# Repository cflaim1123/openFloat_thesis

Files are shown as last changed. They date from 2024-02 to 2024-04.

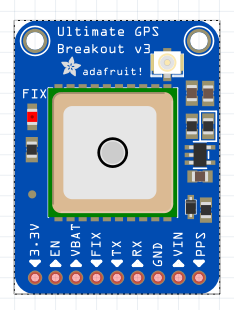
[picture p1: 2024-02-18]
floatBuild/electronics/floatElectronicsFritzingPics/Screenshot 2023-10-19 at 9.54.05 PM.png

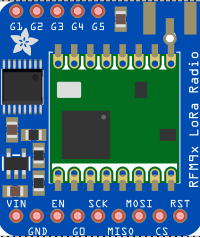
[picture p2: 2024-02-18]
floatBuild/electronics/floatElectronicsFritzingPics/Screenshot 2023-10-19 at 10.49.54 PM.png

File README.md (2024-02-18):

# openFloat
This repository documents the build and implementation of a DIY profiling float for my undergraduate senior thesis at the University of Washington School of Oceanography.
To clone this repository to your working directory, paste the following line into your terminal or command line:
```
git clone https://github.com/cflaim1123/openFloat_thesis.git
```
If you do not have git installed on your machine, follow this [link](https://git-scm.com/downloads) to the git website. 

## Project description
Ocean salinity, a measure of salt concentration in seawater, is a key variable influencing water density and controls important processes like mixing and stratification. Temporal and spatial salinity variability is high in dynamic coastal systems like Puget Sound, which can present a challenge for making salinity measurements that can characterize this variability. Salinity is typically measured using conductivity cells, a sensor that quantifies electrical current through seawater. These sensors can be deployed on ship-based CTDs, spatially-limited moorings, or costly AUVs and can have limited long-term stability. This project, therefore, proposes the development of a cost-efficient DIY profiling float for salinity estimation by way of back-calculation from the TEOS-10 equation of state of seawater. This calculation will be made from known float properties – float density at neutral buoyancy which equals surrounding seawater density – and the in-situ measurement of pressure and temperature via float sensors. This project aims to develop and validate a cost-effective profiling float from common materials with the potential application to increase data resolution in spatially and temporally dynamic estuary systems. For the proof of concept, the float will be deployed alongside a Seaglider in Colvos Passage, WA, for data validation. Unlike many areas of dynamic coastal ecosystems, Colvos Passage experiences high levels of mixing due to local bathymetry and poses as a unique validation site for float development since there is limited spatial variability, making cross-comparison of with the Seaglider easier. This ensures that salinity calculations from the float can be compared to Seaglider data in the same parcel of water to determine the float’s salinity estimation accuracy compared to an industry-standard method for measuring salinity.  

The openFloat will collect pressure and temperature, GPS location, lux, temperature, internal humidity, internal temperature, and internal pressure data. All data will be written to an onboard SD card and transmitted to an onshore radio controller via 915 mHz LoRa (long-range) radio. A digital Onshape CAD model of the openFloat can be found [here](https://cad.onshape.com/documents/a3a60be64346f3ab3cbba062/w/3aa2cdeafc929d436fb9bbdd/e/518a3778be8193c016e5ac27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).

## openFloat Materials
The openFloat is built from 3D-printed and stock hardware and electronics; all parts can be 3D-printed or easily purchased from websites such as [McMaster-Carr](https://www.mcmaster.com/), [Adafruit](https://www.adafruit.com/), [Amazon](https://www.amazon.com/), or [Digikey](https://www.digikey.com/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).

A complete parts and STL file list can be found in this repo's "floatBuild" directory. 

## openFloat Project Concept
The openFloat aims to increase data resolution in dynamic systems by cost-effectively measuring traditional oceanographic data such as temperature, pressure, and salinity. Salinity is not traditionally cheap to measure (e.g., a decent conductivity cell costs ~$5,000).

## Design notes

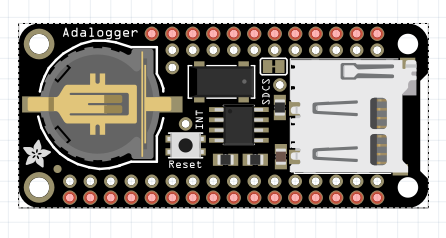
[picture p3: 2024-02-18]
floatBuild/electronics/floatElectronicsFritzingPics/Screenshot 2023-10-19 at 9.54.43 PM.png

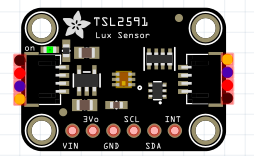
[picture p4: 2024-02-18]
floatBuild/electronics/floatElectronicsFritzingPics/Screenshot 2023-10-19 at 10.00.33 PM.png

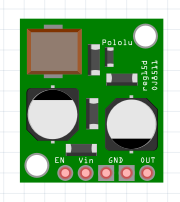
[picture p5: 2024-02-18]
floatBuild/electronics/floatElectronicsFritzingPics/Screenshot 2023-10-19 at 9.55.57 PM.png

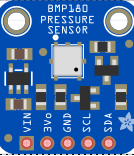
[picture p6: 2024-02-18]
floatBuild/electronics/floatElectronicsFritzingPics/Screenshot 2023-10-20 at 12.47.39 AM.png

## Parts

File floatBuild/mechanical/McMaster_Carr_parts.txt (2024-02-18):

- SCH40 4" PVC pipe (40" length) --> can be bought from any hardware store
- SCH40 4" PVC pipe (9" length?) --> can be bought from any hardware store
- SCH40 1" PVC pipe (25' length) --> can be bought from any hardware store
- 2x Union Straight Connector, 4 Socket-Connect Female (part: 4880K309) 
- 1x Cap, White, 4 Pipe Size Socket-Connect Female (part: 4880K58)
- 1x Bushing Reducing Adapter, 4 Socket Male x 1 Socket Female (part: 4880K072)
- 1x Union Straight Connector, 1 Socket-Connect Female (part: 4880K303)

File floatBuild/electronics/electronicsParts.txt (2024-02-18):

Adafruit 9dof website: https://learn.adafruit.com/adafruit-bno055-absolute-orientation-sensor/arduino-code 

Adafruit pcf8523 RTC: https://learn.adafruit.com/adafruit-adalogger-featherwing/adafruit2-rtc-with-arduino

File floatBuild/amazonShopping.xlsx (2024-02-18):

Store | Item name | Qauntity | total price | link
Amazon | 2-part 24hr epoxy | 1 | 64.89 | https://www.amazon.com/dp/B08XF92PKY
 | 27:1 Geared stepper motor | 1 | 41.91 | https://www.amazon.com/27-Planetary-Gearbox-Stepper-Printer/dp/B00QEUZ9EM
 | TR8x2 800mm lead screw with colar | 1 | 24.99 | https://www.amazon.com/ReliaBot-380mm-Thread-Printer-Machine/dp/B08DJ9JQ6M?s=industrial
 | Tr8x2 brass nut | 1 | 4.99 | https://www.amazon.com/ReliaBot-380mm-Thread-Printer-Machine/dp/B07TZCHP1N?s=industrial
 | TMC2209 stepper drivers | 1 | 26.99 | https://www.amazon.com/BIGTREETECH-Printer-Stepstick-TMC2209-Heatsink/dp/B07YW7BM68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
 | Punching balloon | 1 | 8.39 | https://www.amazon.com/GOLF-Balloons-Assorted-Punching-Wedding/dp/B07F6BFF95
 | 1 gal mineral oil | 1 | 29.99 | https://www.amazon.com/Mineral-Cutting-Butcher-Stainless-Approved/dp/B00VNI1JI0?s=hi
 |  | total: | 202.15

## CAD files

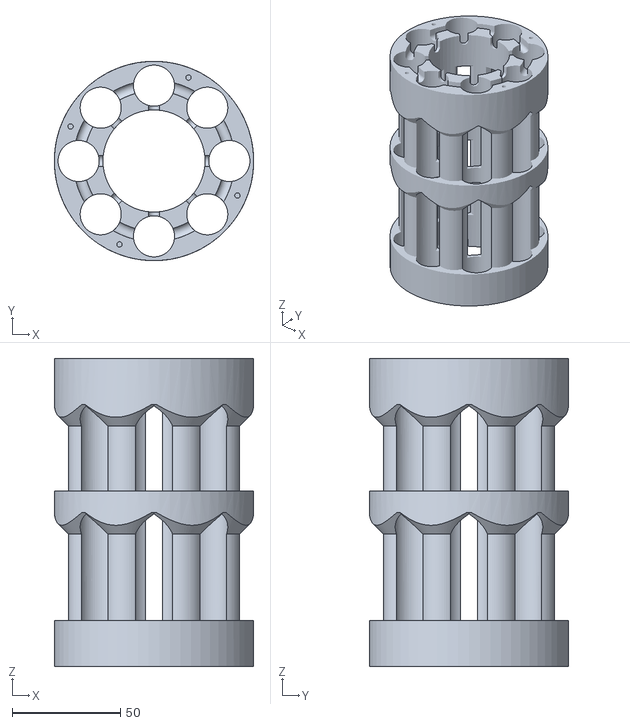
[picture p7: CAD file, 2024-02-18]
floatBuild/mechanical/STLsForPrinting/batteryHolder.stl
92.3 x 92.2 x 142.5

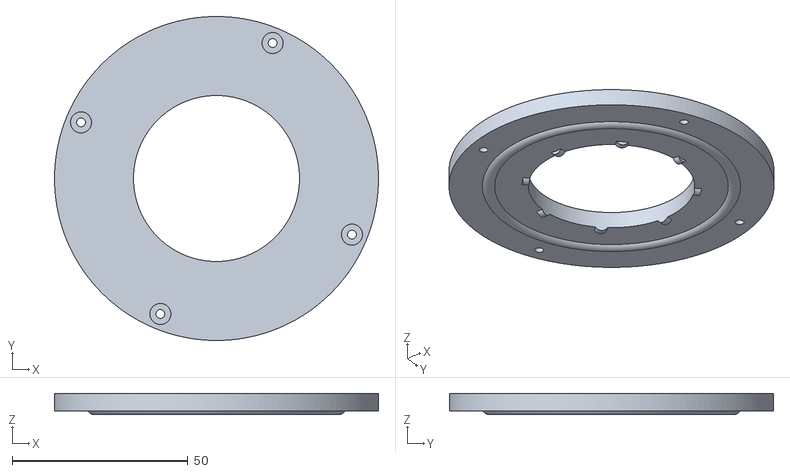
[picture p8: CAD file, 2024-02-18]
floatBuild/mechanical/STLsForPrinting/batteryHolderCap.stl
92.3 x 92.3 x 6.00

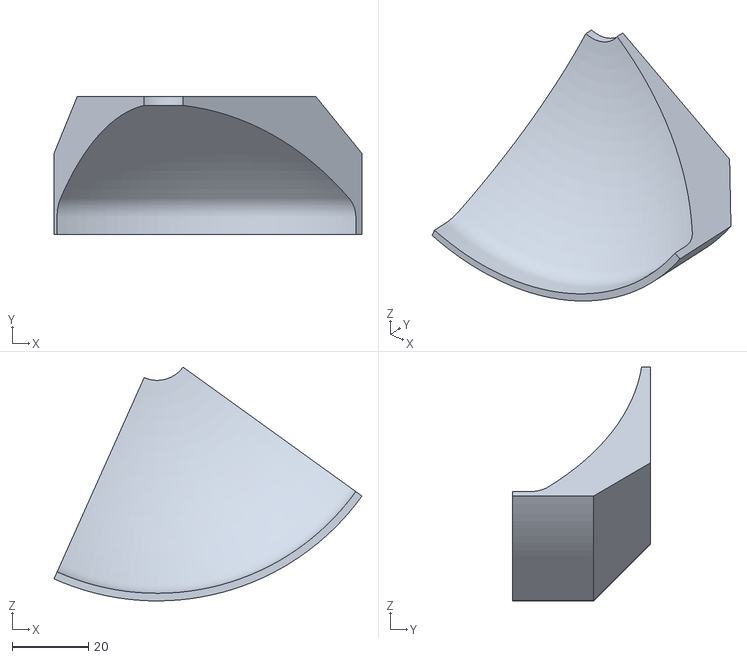
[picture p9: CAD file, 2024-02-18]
floatBuild/mechanical/STLsForPrinting/GpsMountingPlate.stl
81.0 x 36.4 x 61.5

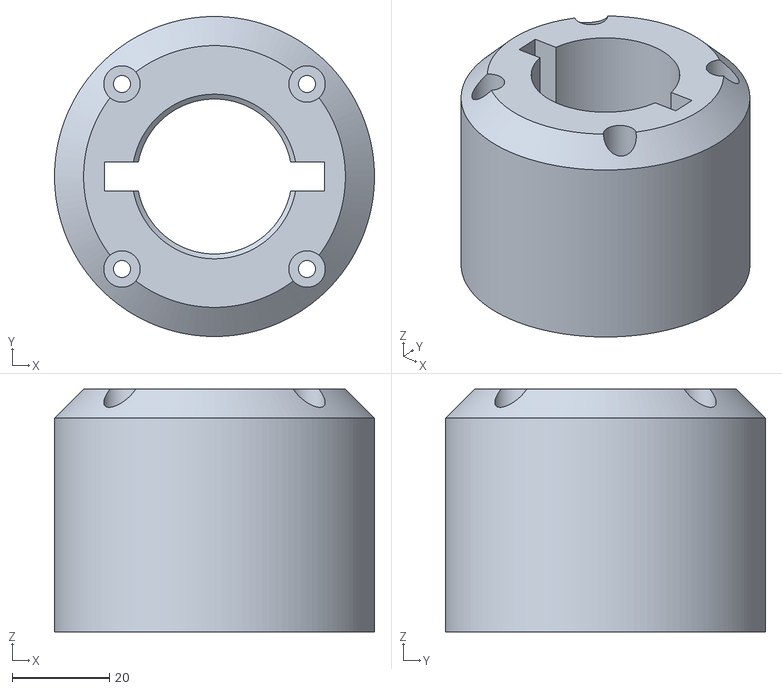
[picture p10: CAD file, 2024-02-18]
floatBuild/mechanical/STLsForPrinting/motorMountFinalTop.stl
65.9 x 65.9 x 50.0

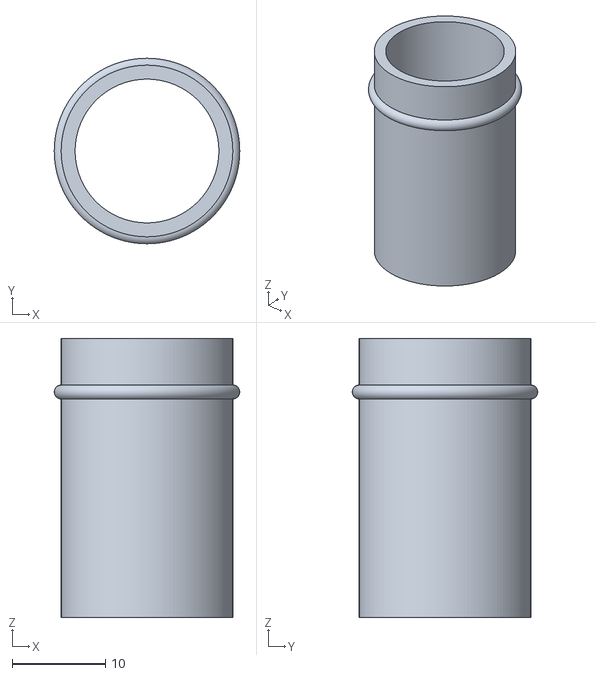
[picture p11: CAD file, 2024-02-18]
floatBuild/mechanical/STLsForPrinting/18.48mmCableGland.stl
20.0 x 20.0 x 30.0

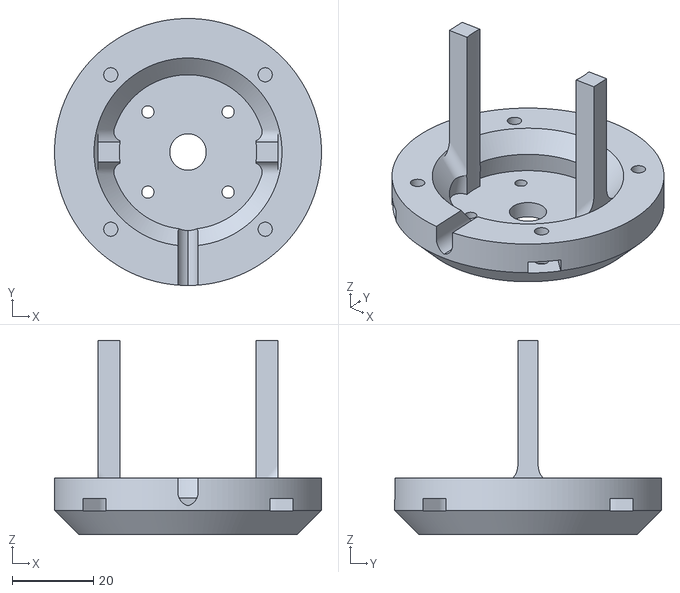
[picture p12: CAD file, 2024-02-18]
floatBuild/mechanical/STLsForPrinting/motorMountFinalBottom.stl
65.9 x 65.9 x 48.0

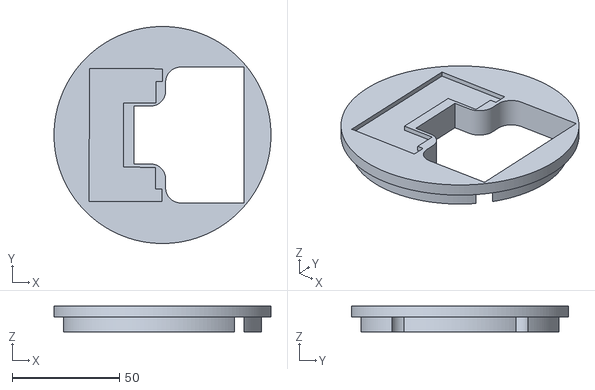
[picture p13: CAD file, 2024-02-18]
floatBuild/mechanical/STLsForPrinting/electronicsHolderBase.stl
101.3 x 101.3 x 12.0

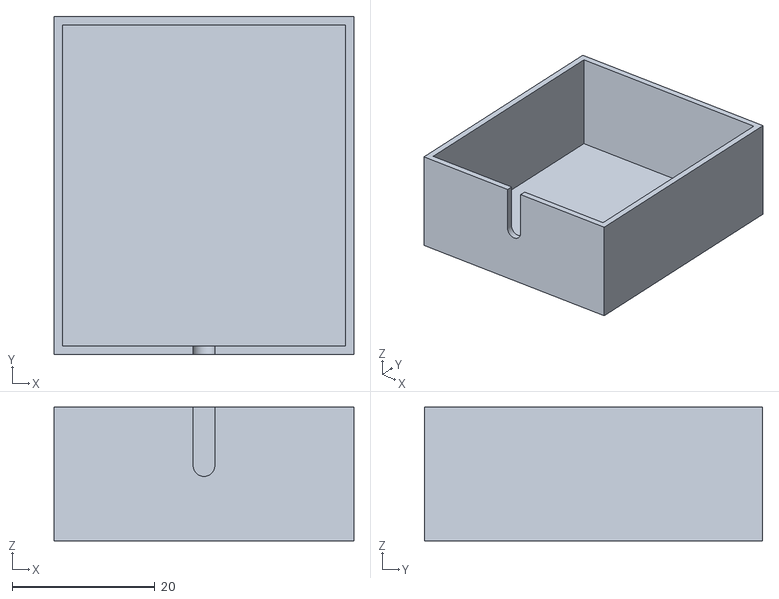
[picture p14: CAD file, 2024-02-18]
floatBuild/mechanical/STLsForPrinting/GpsPottingEdge.stl
42.0 x 47.4 x 18.8

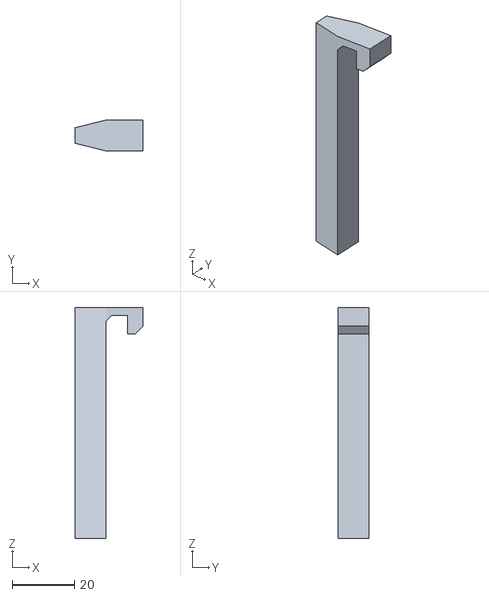
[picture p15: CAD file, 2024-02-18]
floatBuild/mechanical/STLsForPrinting/electronicsHolderClaw.stl
22.1 x 10.0 x 74.5

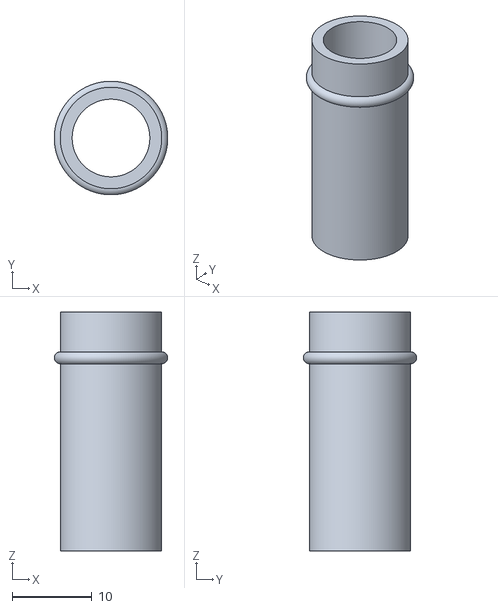
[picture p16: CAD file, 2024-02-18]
floatBuild/mechanical/STLsForPrinting/12.74mmCableGland.stl
14.2 x 14.2 x 30.0

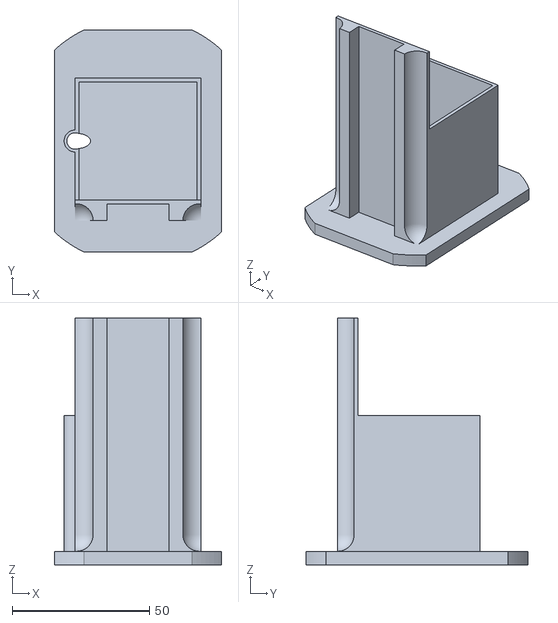
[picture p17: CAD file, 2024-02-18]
floatBuild/mechanical/STLsForPrinting/motorElectronicsMount.stl
61.0 x 81.0 x 90.0

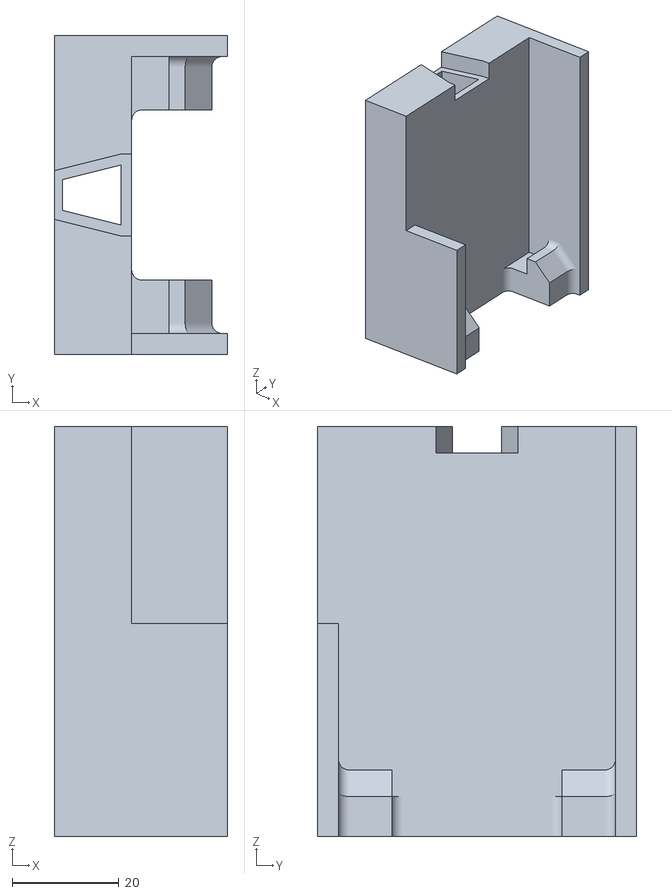
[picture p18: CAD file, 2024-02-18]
floatBuild/mechanical/STLsForPrinting/electronicsHolderSides.stl
32.5 x 60.0 x 77.0

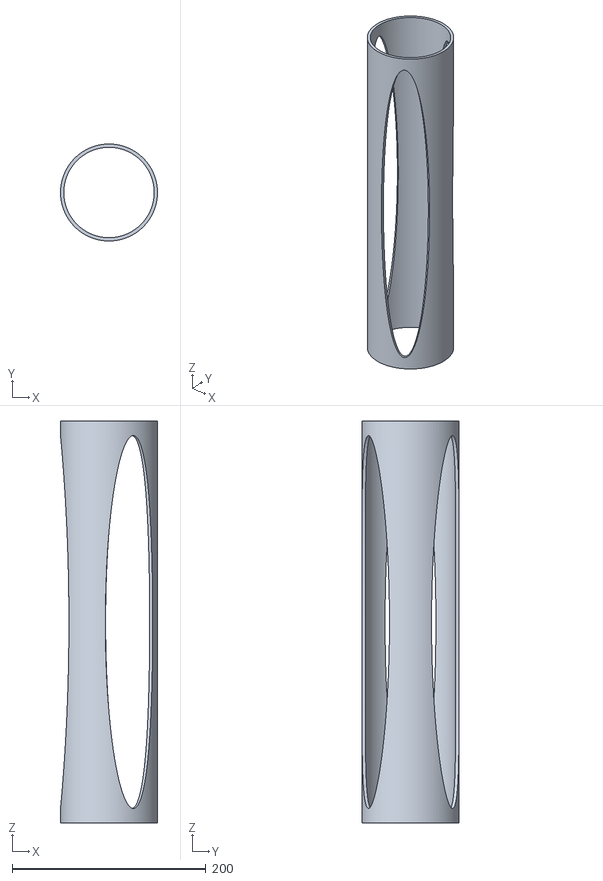
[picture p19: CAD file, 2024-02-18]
floatBuild/mechanical/STLsForPrinting/ElectronicsMountHolder.stl
100.3 x 100.3 x 415.3

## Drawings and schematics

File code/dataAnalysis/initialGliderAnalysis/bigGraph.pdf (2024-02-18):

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

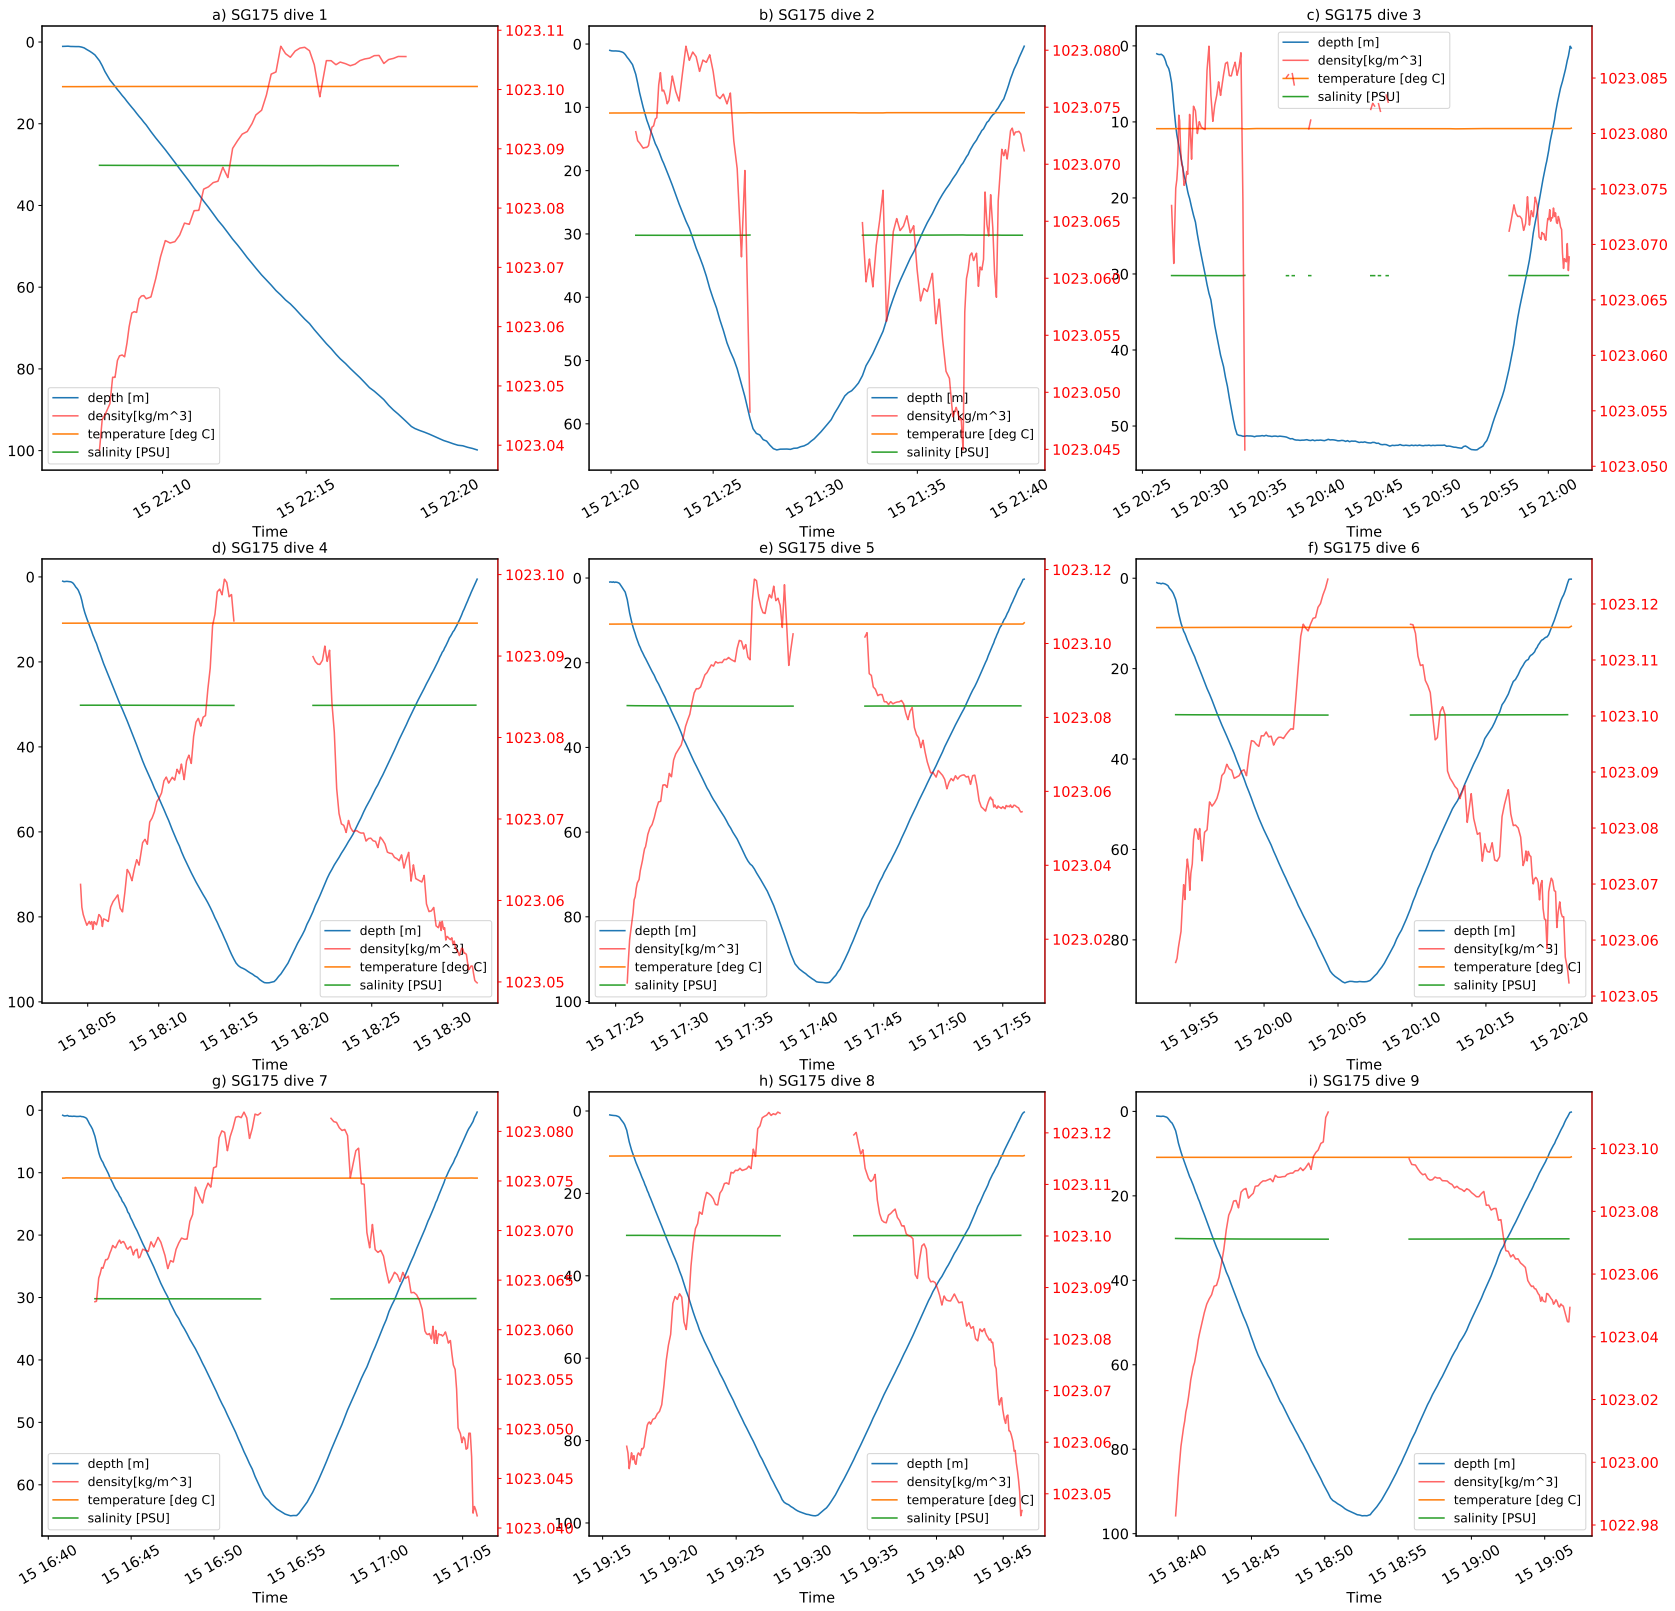
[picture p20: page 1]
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

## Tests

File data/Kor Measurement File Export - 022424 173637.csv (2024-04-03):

Date_(MM/DD/YYYY) | Time_(HH:mm:ss) | Depth_m | Pressure_psi_a | Sal_psu | Temp_C | Vertical_Position_m
2/24/24 | 17:01:37 | 1.98 | 2.882 | 34.64 | 20.384 | 1.998
2/24/24 | 17:02:37 | 2.035 | 2.962 | 34.7 | 20.42 | 2.044
2/24/24 | 17:03:37 | 2.037 | 2.966 | 34.71 | 20.42 | 2.046
2/24/24 | 17:04:37 | 2.038 | 2.967 | 34.71 | 20.421 | 2.044
2/24/24 | 17:05:37 | 2.037 | 2.966 | 34.72 | 20.42 | 2.045
2/24/24 | 17:06:37 | 2.033 | 2.96 | 34.72 | 20.419 | 2.047
2/24/24 | 17:07:37 | 2.029 | 2.954 | 34.72 | 20.419 | 2.042
2/24/24 | 17:08:37 | 2.024 | 2.947 | 34.72 | 20.419 | 2.037
2/24/24 | 17:09:37 | 2.024 | 2.947 | 34.72 | 20.419 | 2.041
2/24/24 | 17:10:37 | 2.021 | 2.942 | 34.72 | 20.419 | 2.032
2/24/24 | 17:11:37 | 2.019 | 2.939 | 34.72 | 20.419 | 2.031
2/24/24 | 17:12:37 | 2.018 | 2.938 | 34.73 | 20.419 | 2.029
2/24/24 | 17:13:37 | 2.017 | 2.936 | 34.73 | 20.419 | 2.029
2/24/24 | 17:14:37 | 2.015 | 2.934 | 34.72 | 20.418 | 2.026
2/24/24 | 17:15:37 | 2.015 | 2.933 | 34.72 | 20.419 | 2.024
2/24/24 | 17:16:37 | 2.014 | 2.933 | 34.73 | 20.419 | 2.024
2/24/24 | 17:17:37 | 2.013 | 2.931 | 34.73 | 20.419 | 2.024
2/24/24 | 17:18:37 | 2.013 | 2.93 | 34.73 | 20.419 | 2.027
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

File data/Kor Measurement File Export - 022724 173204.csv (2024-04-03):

Date_(MM/DD/YYYY) | Time_(HH:mm:ss) | Depth_m | Pressure_psi a | Sal_psu | Temp_C | Vertical_Position_m
2/27/24 | 16:23:01 | 1.782 | 2.594 | 34.74 | 20.136 | 1.801
2/27/24 | 16:23:02 | 1.789 | 2.605 | 34.74 | 20.136 | 1.858
2/27/24 | 16:23:03 | 1.792 | 2.61 | 34.74 | 20.136 | 1.86
2/27/24 | 16:23:04 | 1.81 | 2.636 | 34.74 | 20.136 | 2.003
2/27/24 | 16:23:05 | 1.827 | 2.659 | 34.74 | 20.136 | 2.031
2/27/24 | 16:23:06 | 1.841 | 2.68 | 34.74 | 20.136 | 2.048
2/27/24 | 16:23:07 | 1.853 | 2.698 | 34.74 | 20.137 | 2.041
2/27/24 | 16:23:08 | 1.866 | 2.717 | 34.74 | 20.137 | 2.039
2/27/24 | 16:23:09 | 1.876 | 2.731 | 34.74 | 20.137 | 2.042
2/27/24 | 16:23:10 | 1.884 | 2.744 | 34.74 | 20.137 | 2.039
2/27/24 | 16:23:11 | 1.892 | 2.755 | 34.74 | 20.137 | 2.045
2/27/24 | 16:23:12 | 1.899 | 2.765 | 34.74 | 20.137 | 2.038
2/27/24 | 16:23:13 | 1.907 | 2.776 | 34.74 | 20.137 | 2.038
2/27/24 | 16:23:14 | 1.912 | 2.784 | 34.74 | 20.137 | 2.041
2/27/24 | 16:23:15 | 1.917 | 2.792 | 34.74 | 20.137 | 2.046
2/27/24 | 16:23:16 | 1.922 | 2.799 | 34.74 | 20.137 | 2.037
2/27/24 | 16:23:17 | 1.927 | 2.806 | 34.74 | 20.137 | 2.035
2/27/24 | 16:23:18 | 1.932 | 2.813 | 34.74 | 20.137 | 2.042
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

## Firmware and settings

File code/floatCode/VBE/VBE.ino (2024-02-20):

/*
ESP32 ONLY! RUNS ON TWO CORES.
DOES NOT USE EN PIN, DIRECTLY SOLDERED TO GROUND TO KEEP IT SIMPLE.

SET SPEED, ACCELERATION & CURRENT IN SERIAL TERMINAL LIKE THIS

TO SET SPEED:
-------------
TO SET 1000, INPUT 1000
TO SET 2000, INPUT 2000
MAX 99999, INPUT 99999

ACCELERATION:
-------------
TO SET 1000, INPUT 101000
TO SET 2000, INPUT 102000
MAX 99999, INPUT 199999

CURRENT:
--------
TO SET 100mA, INPUT 200100
TO SET 1000mA, INPUT 201000;
MAX 2000mA, INPUT 202000;

*/

//LIBRARIES THAT YOU NEED
#include <TMCStepper.h>        // https://www.arduino.cc/reference/en/libraries/tmcstepper/
#include "FastAccelStepper.h"  // https://www.arduino.cc/reference/en/libraries/fastaccelstepper/
#include <esp_now.h>
#include <WiFi.h>
          //200 // PHYSICAL STEPS OF MOTOR, NO MICROSTEPS INCLUDED

//SET THESE 3 PER YOUR CONNECTIONS, AND YOU ARE GOOD TO GO!:
#define DIR_PIN 25          // Direction
#define STEP_PIN 26         // Step
#define SERIAL_PORT Serial  // HardwareSerial port
#define EN_PIN 21
#define STALL_VALUE 255      // [0..255]
#define DRIVER_ADDRESS 0b00  // TMC2209 Driver address according to MS1 and MS2
#define R_SENSE 0.11f        // 0.11 for MKS TMC2209

int MAX_BUOY = 0;
int C_VBE = 125;
int MIN_BUOY = 250;

float current_pos = 0;
float move_pos;

//DEFINE YOUR STARTING VALUES!
int AMPS = 1680;    // SET STARTING CURRENT MAX 2000
int micro = 0;      // SET MICROSTEPS
int Maccell = 500;  // SET STARTING ACCELERATION
int Mspeed = 8000;  // SET STARTING STEPS/S
int MMperRev = 8;   // SET MM PER REVOLUTION
int movemm = 250; //304.8;
int moveMM = MMperRev * movemm - 4.75;  //304.8; // SET MOVEMENT IN MM
int StepsPerRoation = 5373; 

TMC2209Stepper driver(&SERIAL_PORT, R_SENSE, DRIVER_ADDRESS);
using namespace TMC2209_n;


FastAccelStepperEngine engine = FastAccelStepperEngine();
FastAccelStepper *stepper = NULL;

unsigned long howLong = 0;

TaskHandle_t Motor;
TaskHandle_t Print;
TaskHandle_t Input;

void setup() {
  // INTITIALIZE SERIAL0 ITERFACE
  Serial.begin(115200);
  WiFi.mode(WIFI_STA);
 
  // Initilize ESP-NOW
  if (esp_now_init() != ESP_OK) {
    Serial.println("Error initializing ESP-NOW");
    return;
  }
  
  // Register callback function
  esp_now_register_recv_cb(OnDataRecv);
  // digitalWrite(EN_PIN, HIGH);
  // delay(600000);
  Serial.println(F("---------------------------------------------------"));
  Serial.println(F("UART0 serial output interface intitialized @ 115200"));
  // INITIALIZE SERIAL2 UART FOR TMC2209
  SERIAL_PORT.begin(115200);  //,SERIAL_8N1, 16, 17
  Serial.println(F("UART2 interface for TMC2209 intitialized   @ 115200"));
  Serial.println(F("---------------------------------------------------"));

  //TMCSTEPPER SETTINGS
  driver.begin();

  driver.toff(2);         // [1..15] enable driver in software
  driver.blank_time(24);  // [16, 24, 36, 54]

  driver.hysteresis_start(1);  // [1..8]
  driver.hysteresis_end(12);   // [-3..12]



  driver.rms_current(AMPS, 0.01);  // motor RMS current "rms_current will by default set ihold to 50% of irun but you can set your own ratio with additional second argument; rms_current(1000, 0.3)."

  driver.seimin(1);  // minimum current for smart current control 0: 1/2 of IRUN 1: 1/4 of IRUN

  driver.semin(15);  // [0... 15] If the StallGuard4 result falls below SEMIN*32, the motor current becomes increased to reduce motor load angle.
  driver.semax(15);  // [0... 15]  If the StallGuard4 result is equal to or above (SEMIN+SEMAX+1)*32, the motor current becomes decreased to save energy.

  driver.sedn(4);  // current down step speed 0-11%
  driver.seup(2);  // Current increment steps per measured StallGuard2 value 5 seup0 %00 … %11: 1, 2, 4, 8

  driver.iholddelay(3);  // 0 - 15 smooth current drop

  driver.TPWMTHRS(0);  // 0: Disabled, 0xFFFFF = 1048575 MAX TSTEP.
                       // StealthChop PWM mode is enabled, if configured. When the velocity exceeds
                       // the limit set by TPWMTHRS, the driver switches to SpreadCycle.

  driver.TCOOLTHRS(0);           // 0-7 TSTEP
                                 // 0: TPWM_THRS= 0
                                 // 1: TPWM_THRS= 200
                                 // 2: TPWM_THRS= 300
                                 // 3: TPWM_THRS= 400
                                 // 4: TPWM_THRS= 500
                                 // 5: TPWM_THRS= 800
                                 // 6: TPWM_THRS= 1200
                                 // 7: TPWM_THRS= 4000
  driver.pwm_autoscale(true);    // Needed for stealthChop
  driver.en_spreadCycle(false);  // false = StealthChop / true = SpreadCycle


  driver.microsteps(micro);  // microsteps
  driver.shaft(false);       // direction
  driver.intpol(true);       // interpolate to 256 microsteps
  //driver.ihold(2);               // hold current  0=1/32 … 31=32/32
  //driver.irun(31);
  driver.SGTHRS(STALL_VALUE);
  //driver.I_scale_analog(0);   // if 5v vdd

  //ACCELL STEPPER SPEED & ACCELERATION
  engine.init();
  stepper = engine.stepperConnectToPin(STEP_PIN);
  stepper->setDirectionPin(DIR_PIN);
  stepper->setSpeedInHz(Mspeed);  // STEPS PER SECOND
  stepper->setAcceleration(Maccell);

  if (micro != 0) { StepsPerRoation = StepsPerRoation * micro; };

  xTaskCreatePinnedToCore(PrintTask, "Print", 2000, NULL, tskIDLE_PRIORITY, &Print, 1);
  xTaskCreatePinnedToCore(MotorTask, "Motor", 5000, NULL, 5, &Motor, 0);
  xTaskCreatePinnedToCore(InputTask, "Input", 5000, NULL, 2, &Input, 1);
}

void loop() {
  vTaskDelete(NULL);
}

//PRINT SERIAL--------------------------------------------------
void OnDataRecv(const uint8_t * mac, const uint8_t *incomingData, int len) {
  memcpy(&move_pos, incomingData, sizeof(move_pos));
  // move_pos = incomingData;
  if(move_pos == current_pos){
    move_pos = current_pos;
  }
  else if(move_pos > MIN_BUOY){
    move_pos = current_pos;
  }
  else if(move_pos < MAX_BUOY){
    move_pos = current_pos;
  }
}
void PrintTask(void *) {
  int SSpeed;
  int steppes;
  float ActualSpeed;
  float MaxSpeed;
  for (;;) {

    steppes = driver.TSTEP();
    SSpeed = 12000000. / (steppes * 256.);
    ActualSpeed = (SSpeed / StepsPerRoation) * MMperRev;

    if (ActualSpeed > MaxSpeed) { MaxSpeed = ActualSpeed; };
    if (ActualSpeed == 0) { MaxSpeed = 0; };



    Serial.print("ACTUAL");
    Serial.print(F(" / "));
    Serial.print("MAX");
    Serial.print(F(" / "));
    Serial.print("AVARAGE");
    Serial.print(F(" / "));
    Serial.println("REQUESTED");
    Serial.print(ActualSpeed, 2);
    Serial.print(F(" / "));
    Serial.print(MaxSpeed, 2);
    Serial.print(F(" / "));
    Serial.print((moveMM / (howLong / 1000.)), 2);
    Serial.print(F(" / "));
    Serial.print((Mspeed / StepsPerRoation) * MMperRev, 2);
    Serial.println(F(" MM/S"));
    Serial.print(SSpeed);
    Serial.print(" / ");
    Serial.print(MaxSpeed / (MMperRev / StepsPerRoation), 0);
    Serial.print(" / ");
    Serial.print((moveMM / (MMperRev / StepsPerRoation)) / (howLong / 1000.), 0);
    Serial.print(" / ");
    Serial.print(Mspeed);
    Serial.println(F(" STEPS/S"));
    Serial.print(60. * (SSpeed / StepsPerRoation), 0);
    Serial.print(" / ");
    Serial.print(60. * ((MaxSpeed / (MMperRev / StepsPerRoation)) / StepsPerRoation), 0);
    Serial.print(" / ");
    Serial.print((((moveMM / (MMperRev / StepsPerRoation)) / (howLong / 1000.)) / StepsPerRoation) * 60., 0);
    Serial.print(" / ");
    Serial.print(60. * (Mspeed / StepsPerRoation), 0);
    Serial.println(F(" RPM"));
    Serial.print(Maccell);
    Serial.println(F(" ACCELERATION"));
    Serial.println("----------------------------------");
    Serial.print(driver.cs2rms(driver.cs_actual()), DEC);
    Serial.print(" / ");
    Serial.print(AMPS);
    Serial.println(" MA MOTOR CURRENT");
    Serial.print(stepper->getCurrentPosition());
    Serial.print(" / ");
    Serial.print(stepper->targetPos());
    Serial.println(" STEP POSITION");
    Serial.print(driver.SG_RESULT());
    Serial.println(" STALLGUARD");
    Serial.print(steppes);
    Serial.println(" TSTEP");
    Serial.print(float(howLong / 1000.), 2);
    Serial.println("S LAST MOVEMENT DURATION");
    Serial.print(driver.microsteps());
    Serial.println(F(" MICROSTEPS"));

    Serial.println("----------------------------------");

    vTaskDelay(100);
  }
}

//CHECK FOR SERIAL COMMANDS--------------------------------------------------------

void InputTask(void *) {

  for (;;) {

    int dataIn = 0;

    if (Serial.available()) {
      dataIn = Serial.parseInt();

      if (dataIn > 0 && dataIn < 10000) {
        Mspeed = dataIn;
        stepper->setSpeedInHz(Mspeed);
      };

      if (dataIn >= 100000 && dataIn < 200000) {
        Maccell = dataIn - 10000;
        stepper->setAcceleration(Maccell);
      };

      if (dataIn >= 200000 && dataIn <= 202001) {
        AMPS = dataIn - 200000;
        driver.rms_current(AMPS, 0.01);
      };
    };
    vTaskDelay(5);
  }
}

//MOTOR--------------------------------------------------------

void MotorTask(void *) {
  // digitalWrite(EN_PIN, HIGH);
  vTaskDelay(10000);
  // digitalWrite(EN_PIN, LOW);
  int loop_cnt = 1;
  for (;;) {
    unsigned long timeIs = millis();
        stepper->moveTo((move_pos * MMperRev - 4.75) / (MMperRev / StepsPerRoation), true);  // TRUE makes this a blocking function. Remove it to use it as non blocking.
        howLong = millis() - timeIs;
        vTaskDelay(3000);


    // if(loop_cnt == 1){
    //     // Move to 250mm distance (Max buoyancy)
    //     stepper->moveTo((MAX_BUOY * MMperRev - 4.75) / (MMperRev / StepsPerRoation), true);  // TRUE makes this a blocking function. Remove it to use it as non blocking.
    //     howLong = millis() - timeIs;
    //     vTaskDelay(3000);

    // } else if(loop_cnt == 1){
    //     // Move to 125mm distance (C_VBE??)
    //     stepper->moveTo((-C_VBE * MMperRev + 4.75) / (MMperRev / StepsPerRoation), true);  // TRUE makes this a blocking function. Remove it to use it as non blocking.
    //     howLong = millis() - timeIs;
    //     vTaskDelay(3000);
    // } else if(loop_cnt == 2){
    //     // Move to 0mm distance (Min buoyancy)
    //     stepper->moveTo((-MIN_BUOY * MMperRev + 4.75) / (MMperRev / StepsPerRoation),true); //
    //     vTaskDelay(3000);
    // }
    // loop_cnt++;
    // if(loop_cnt > 2){ loop_cnt = 0;}
  }
}

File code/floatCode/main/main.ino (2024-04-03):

////////// sensors and electronics on board //////////
// board 1
// - pcf8523 RTC
// - microsd reader
// - BNO055 9-axis abosute postioning IMU
// - BMP180 temperature and pressure
// board 2
// - adafruit ultimate gps
// board 3
// 915 mhz LoRa module
// board 4
// - DHT22 temperature and humidity
// - DS18b20 temperature probe (x3)
// - NTC 10K Thermistor
// - MS8503-05 BA
// - TSl2591 lux sensor
// board 5
// - INA219 current meter
// - pololu 5V 5A step-down converter


#include <Wire.h>
#include "SPI.h"
#include <esp_now.h>
#include <wifi.h>
// #include <OneWire.h>

#include <Adafruit_Sensor.h>

// internal humidity
#include <DHT.h>
#include <DHT_U.h>
// IMU
#include <Adafruit_BNO055.h>
#include <utility/imumaths.h>
// internal pressure
#include <SFE_BMP180.h>
// sd card reader and clock backpack
#include "RTClib.h"
#include "FS.h"
#include <SD.h>
// GPS
#include <Adafruit_GPS.h>
// External pressure
#include "MS5803_05.h"
// Radio
#include <LoRa.h>
// Lux sensor
#include "Adafruit_TSL2591.h"
// external temp
// #include <DallasTemperature.h>

#define MOVE_SAMPLE_RATE 300   // millisecods
#define IDLE_SAMPLE_RATE 3000  // milliseconds
#define N_DIVES 1
#define TIME_AT_DEPTH 300000
#define TIME_AT_SURF 600000
#define ABORT_DEPTH 50 // dbar
#define T_DEPTH 25 // dbar

////////// GPS serial port //////////
#define GPSSerial Serial1
////////// sensors pins //////////
// External digital temp
#define ONE_WIRE_BUS 37
// Internal temp and humidity
#define DHT22_DATA_PIN 15
// Internal pressure
#define BMP180_power 32  // need to make sure sensor is grounded to controller
// SD reader
#define SD_CS 33  //const int8_t SD_CS = 33;
// Radio
#define RADIO_CS 12
#define RADIO_EN 25   // A1
#define RADIO_GO 13   // desolderd
#define RADIO_RST 27  // desoldered
// GPS
#define GPS_EN 26  // A0
// Thermistor
#define THERMISTOR_ADC 36  // A4

#define DHTTYPE DHT22

uint64_t floatStart = millis();
unit64_t current_elapsed_t_at_depth = 0;
uint8_t broadcastAddress[] = { 0xE8, 0x9F, 0x6D, 0x2F, 0x1B, 0x6C };
int current_pressure;
int last_pressure ;
int delta_pressure;
esp_now_peer_info_t peerInfo;
DateTime now;
const uint8_t missionNum = 0;
char globalTime[] = "%02d/%02d/%02d %02hhu:%02hhu:%02hhu";
char dataSavePath[32];

// OneWire oneWire(ONE_WIRE_BUS);
////////// create sensor suit //////////

// make sensor objects
// board 1
Adafruit_BNO055 bno = Adafruit_BNO055(55, 0x28, &Wire);
SFE_BMP180 bmp180;
RTC_PCF8523 rtc;
Adafruit_GPS GPS(&GPSSerial);
DHT_Unified dht(DHT22_DATA_PIN, DHTTYPE);
MS_5803 ms5803 = MS_5803(512);
// Adafruit_TSL2591 tsl = Adafruit_TSL2591(2591);
// DallasTemperature sensors(&oneWire); //one wire doesn't appear to work on this board https://github.com/adafruit/circuitpython/issues/7434

// Make data structure to hold float sensor values
struct FloatData {
  uint64_t codeStartTime = floatStart;
  DateTime turnOnTime;
  float initial_initernal_pressure;
  float initial_initernal_humidity;

  struct Bmp180Reading {
    float temp, press;

  } bmp180Reading;

  struct Time {
    DateTime dateAndTime;
  } time;

  struct AccelerometerReading {
    int8_t boardTemp;

    struct Orientation {
      float X, Y, Z;
    } orientation;

    struct Gyro {
      float X, Y, Z;
    } gyro;

    struct Linear {
      float X, Y, Z;
    } linear;

    struct Mag {
      float X, Y, Z;
    } mag;

    struct Accl {
      float X, Y, Z;
    } accl;

    struct Gravity {
      float X, Y, Z;
    } gravity;
  } accelerometerReading;

  struct GpsReading {
    DateTime time;
    // uint8_t hour, minute, seconds, day, month;
    // uint16_t year;
    float latitude, longitude, speed, altitude;
    // float angle;
    uint8_t fixquality;
    // unint8_t fix, satellites, antenna;
  } gpsReading;

  struct ThermReadng {
    float temp;
  } thermReading;

  struct Ms5803Reading {
    float temp, press;
  } ms5803Reading;
} floatData;

enum GoNoGoState {
  ABORT,
  ALL_CLEAR
};

enum DiveState {
  IDLE,
  PUMP,
  BLEED,
  MOVING,
  SURFACE
};

GoNoGoState go_no_go_state = ABORT;
DiveState current_state = SURFACE;

/*******************************************************************************/
////////// main loop //////////
void setup() {
  Serial.begin(115200);
  delay(50);
  // Set ESP32 as a Wi-Fi Station
  WiFi.mode(WIFI_STA);
  delay(50);
  initEspNow();
  delay(50);
  Serial1.begin(9600);
  delay(100);
  SPI.begin(SCK, MISO, MOSI, SD_CS);
  delay(100);
  Wire.begin();
  // digitalWrite(12, HIGH);
  LoRa.setPins(RADIO_CS);  // set lora cspin for shutting it off purposes
  delay(100);
  shutOffTheRadio();
  delay(100);             // Work around so that SD card works
  digitalWrite(25, LOW);  // Turn off Radio power
  delay(100);
  init();
}

void loop() {
  uint64_t time = millis();
  updateGoNoGoState();
  processGoNoGoState();
  updateDiveState();
  processDiveState();
  sample();
  delay(100);
  writeToFile(dataSavePath);
  current_pressure = floatData.ms5803Reading.press;
  // delay(50);
  // printEverything();

  if (current_state == PUMP || current_state == BLEED) {
    delay(MOVE_SAMPLE_RATE);
  } else {
    delay(IDLE_SAMPLE_RATE);
  }
  current_elapsed_t_at_depth += time;
  last_pressure = current_pressure;
  delta_pressure = current_pressure - last_pressure;
}

/*******************************************************************************/
/////////ESP now callback ////////////
void OnDataSent(const uint8_t *mac_addr, esp_now_send_status_t status) {
  Serial.print("\r\nLast Packet Send Status:\t");
  Serial.println(status == ESP_NOW_SEND_SUCCESS ? "Delivery Success" : "Delivery Fail");
}

/*******************************************************************************/
/////////State machines ////////////
void updateDiveState() {
  if(current_elapsed_t_at_depth > TIME_AT_DEPTH && current_state == IDLE) {
    current_state = PUMP;
    current_elapsed_t_at_depth = 0;
  } else if(current_elapsed_t_at_depth > TIME_AT_SURFACE && current_state == SURFACE){
    current_state = BLEED;
    current_elapsed_t_at_depth = 0;
  } else if(delta_pressure <= 0.1*current_pressure || delta_pressure >= 0.1*current_pressure){}
}

void processDiveState() {
  switch (current_state) {
    case IDLE:
      Serial.println("Current state is idle!");
      break;
    case PUMP:
      Serial.println("Float is pumping!");
      break;
    case BLEED:
      Serial.println("Float is bleeding!");
      break;
    case SURFACE:
      Serial.println("Float is at the surface!");
      break;
    default:
      break;
  }
}

void updateGoNoGoState() {
  if (floatData.bmp180Reading.press >= floatData.initial_initernal_pressure + 2) {
    go_no_go_state = ABORT;
  } else if (floatData.bmp180Reading.temp >= floatData.initial_initernal_humidity + 10) {
    go_no_go_state = ABORT;
  } else {
    go_no_go_state = ALL_CLEAR;
  }
}
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

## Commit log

2024-02-12 Added data anlaysis code and associated data
    [ExoSondeCtdCastsDec15.csv, SG175_dive_1.csv, SG175_dive_1_sal_estimation.csv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]
2024-02-18 added STL files
    [12.74mmCableGland.stl, 18.48mmCableGland.stl, ElectronicsMountHolder.stl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]
2024-04-03 updated data files
    [Kor Measurement File Export - 022424 173637.csv, Kor Measurement File Export - 022724 173204.csv, floatTankData.csv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]
